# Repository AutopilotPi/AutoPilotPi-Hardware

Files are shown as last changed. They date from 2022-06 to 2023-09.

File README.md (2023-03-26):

# [ENGLISH](https://github.com/Ncerzzk/AutoPilotPi-Hardware/blob/master/README_EN.md)
# AutoPilotPi-Hardware

AutoPilotPi 是一个能够运行 PX4 等自动驾驶固件的单板计算机(SBC)。与通用的 SBC（如树莓派）不同，AutoPilotPi 集成了多种传感器（IMU、磁罗盘、气压计等），因此无需额外的接线即可使用，对于微型飞行器和电路洁癖患者来说非常友好。

AutoPilotPi 使用 V3s 处理器，虽然 V3s 不是性能强大的处理器，但如果能够证明 PX4 能在这些性能较弱的 Linux 处理器上运行，则对于性能更强的处理器来说更加不在话下了。

与传统基于 MCU 的自动驾驶固件不同，使用 Linux 系统的优势在于支持更多的开发语言和工具链，可以更方便地进行二次开发和调试。同时，开启了软实时后的内核基本可以满足 PX4 的实时性要求。

## 接口与传感器

- ICM20600：六轴惯性测量单元
- QMC5883L：三轴磁罗盘
- SPL06：气压高度传感器
- 3 个串口(U0、U1、U2，其中 U0 用于 Linux 调试)
- 1 个 I2C 接口
- 1 个 SPI 接口
- 最多 9 个 PWM 通道

## 特点

- 封装对手焊友好 (EQFP-128)
- 内置 DRAM
- 价格较为便宜

## 相关项目

- V3s 的 Linux 内核：https://github.com/Ncerzzk/linux
- 使用该项目的四旋翼飞行器 (WIP)：https://github.com/Ncerzzk/V3s_Quadrotor
- 该项目的 PX4 分支（部分提交尚未被官方 PX4 接受）：https://github.com/Ncerzzk/PX4-Autopilot
- FPGA 的 HDL 代码：https://github.com/Ncerzzk/I2C_PWM
- Wiki：https://github.com/Ncerzzk/AutoPilotPi-Hardware/wiki

## Images
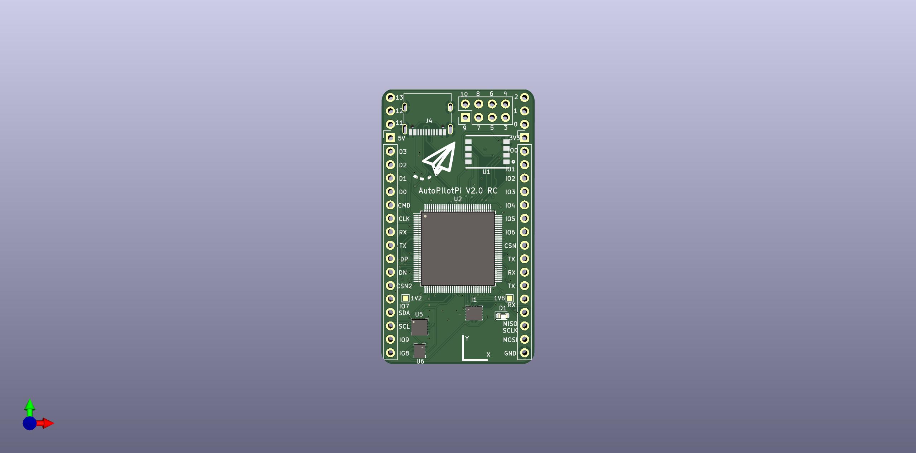
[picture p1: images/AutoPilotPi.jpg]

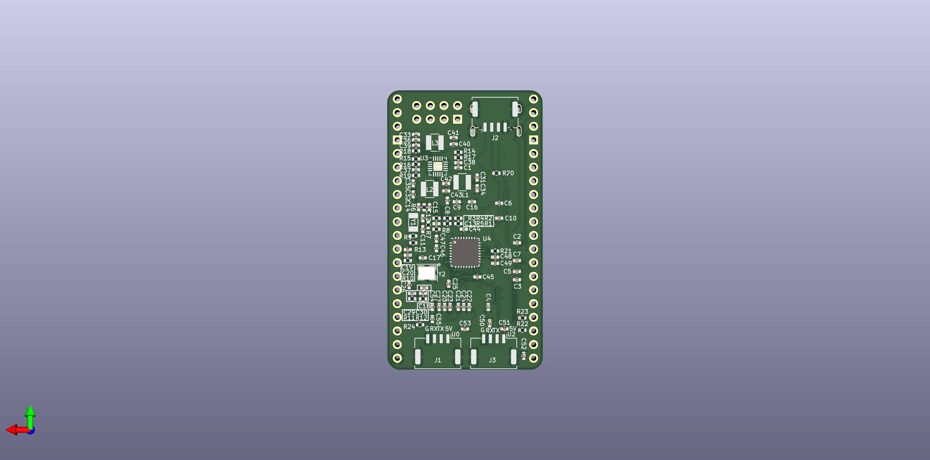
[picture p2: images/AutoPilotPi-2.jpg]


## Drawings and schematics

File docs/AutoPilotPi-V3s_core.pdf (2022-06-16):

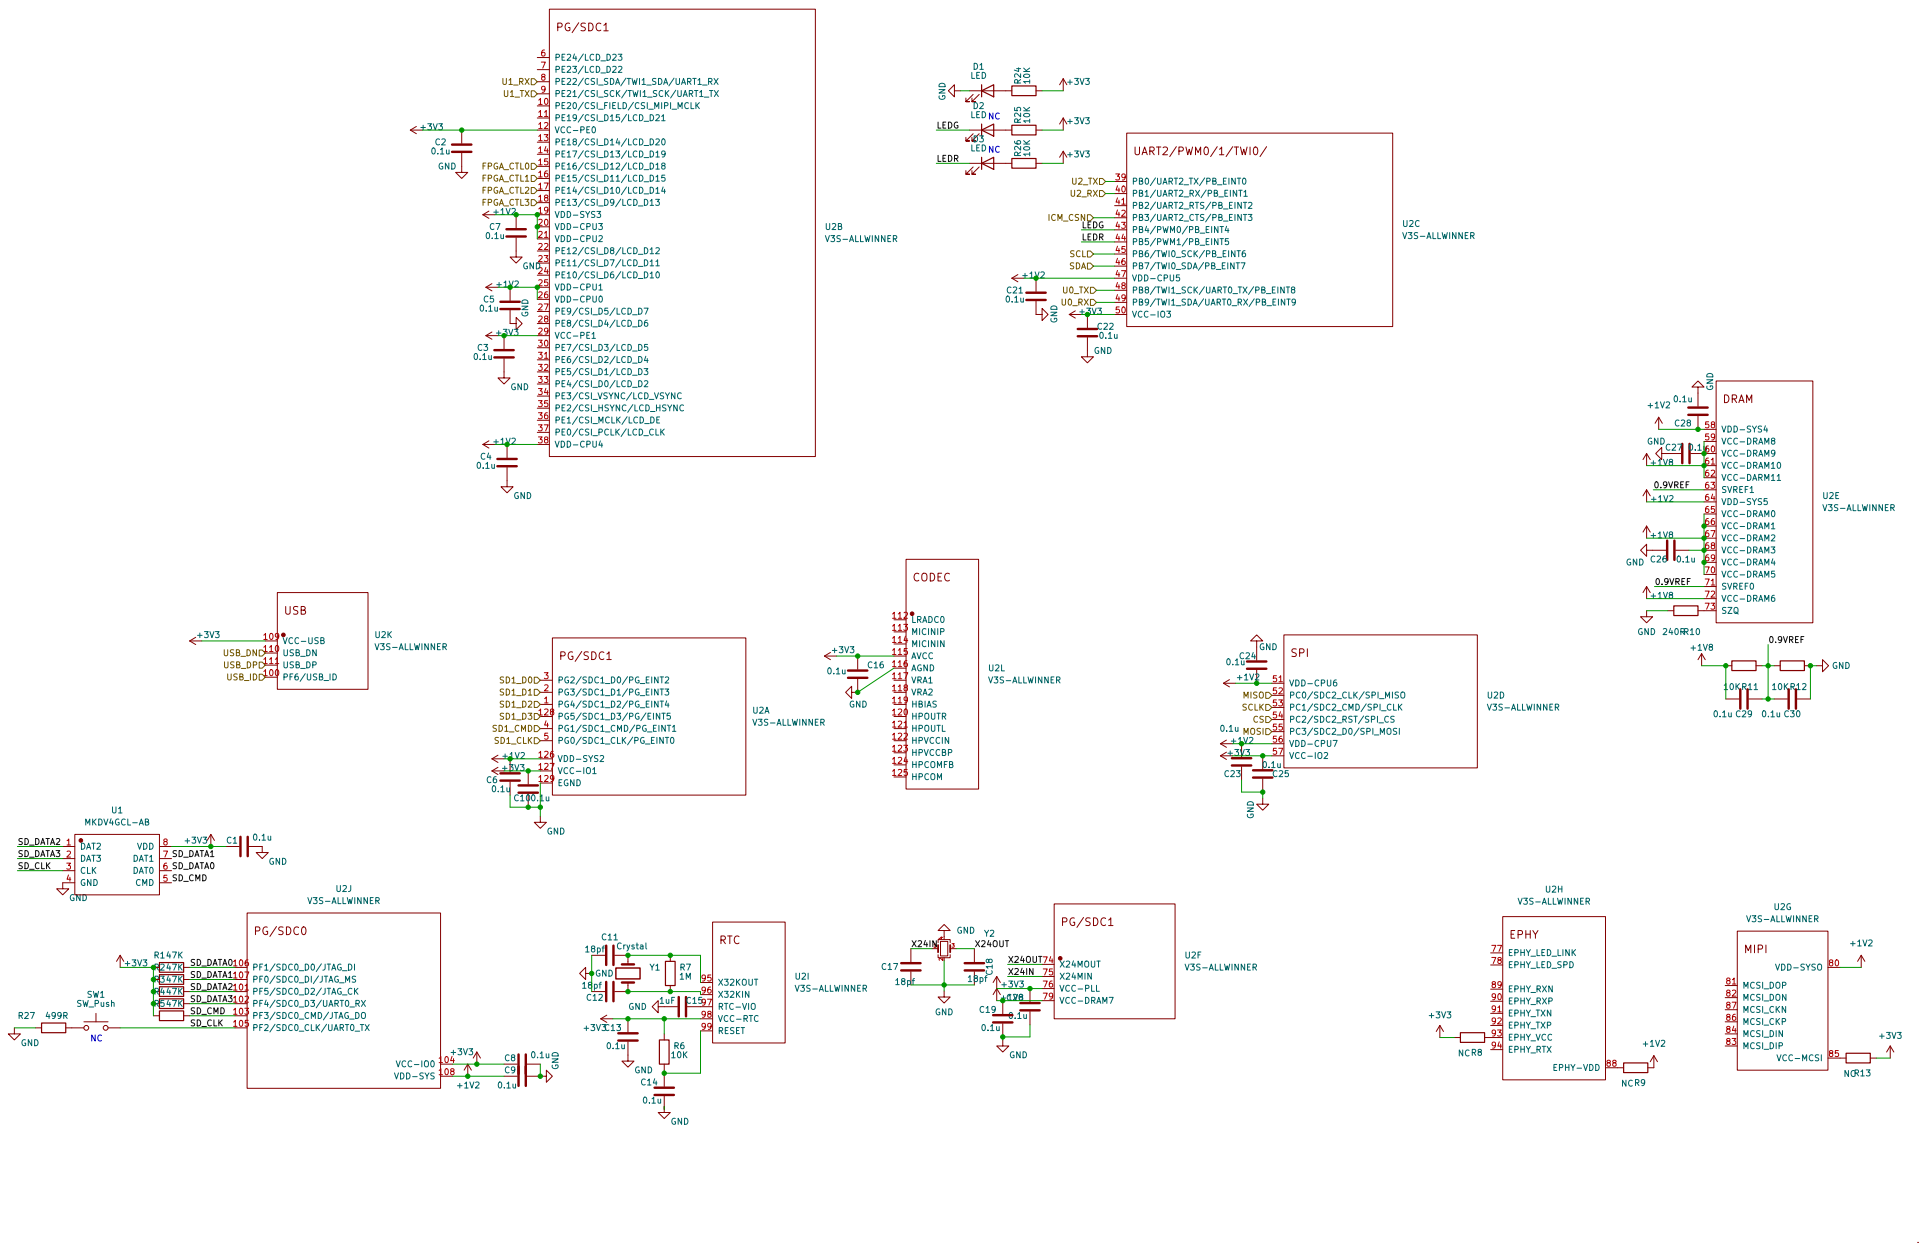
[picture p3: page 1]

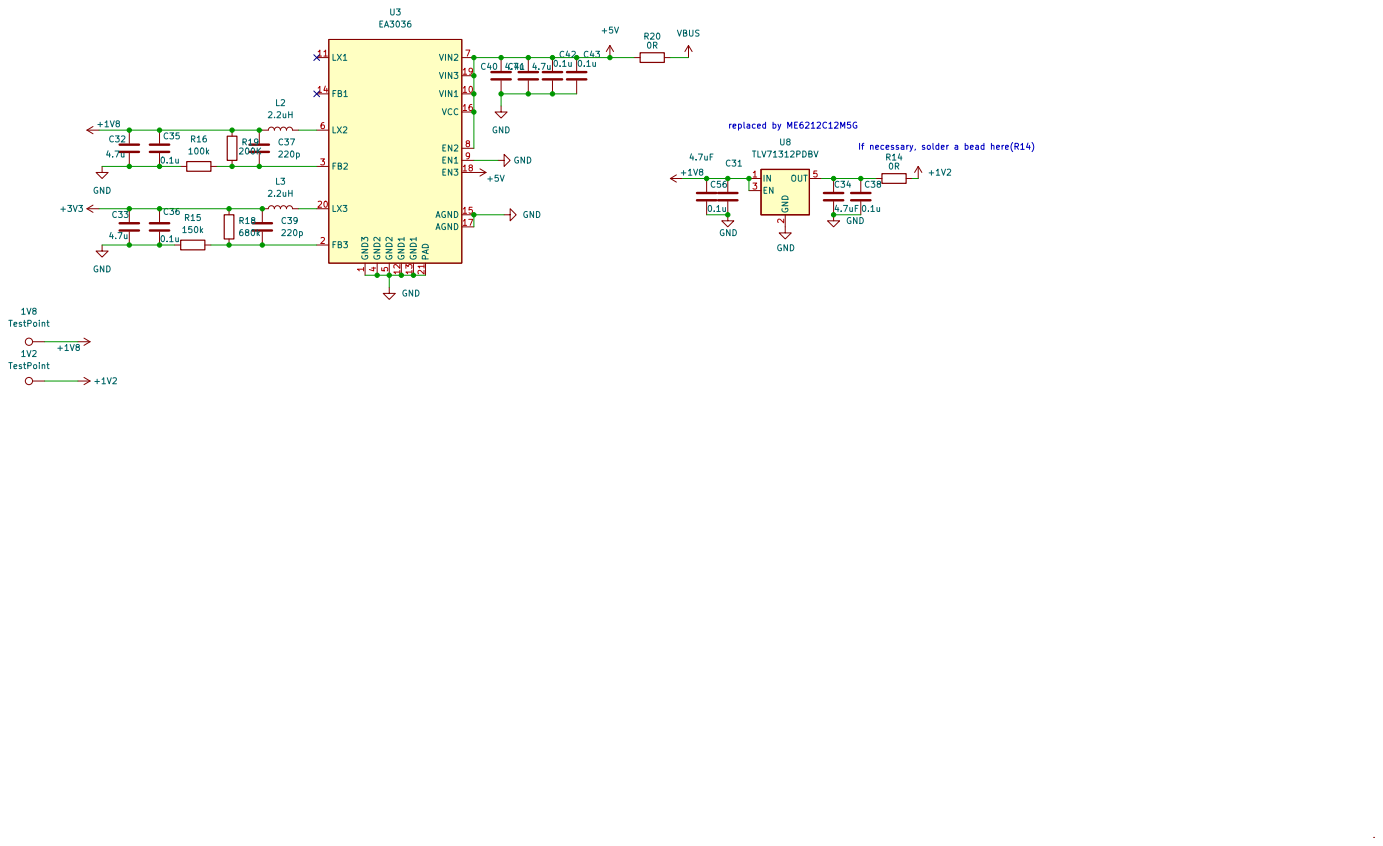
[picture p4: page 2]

2 EN 3 OUT 5 U8 TLV71312PDBV GND GND

If necessary, solder a bead here(R14)

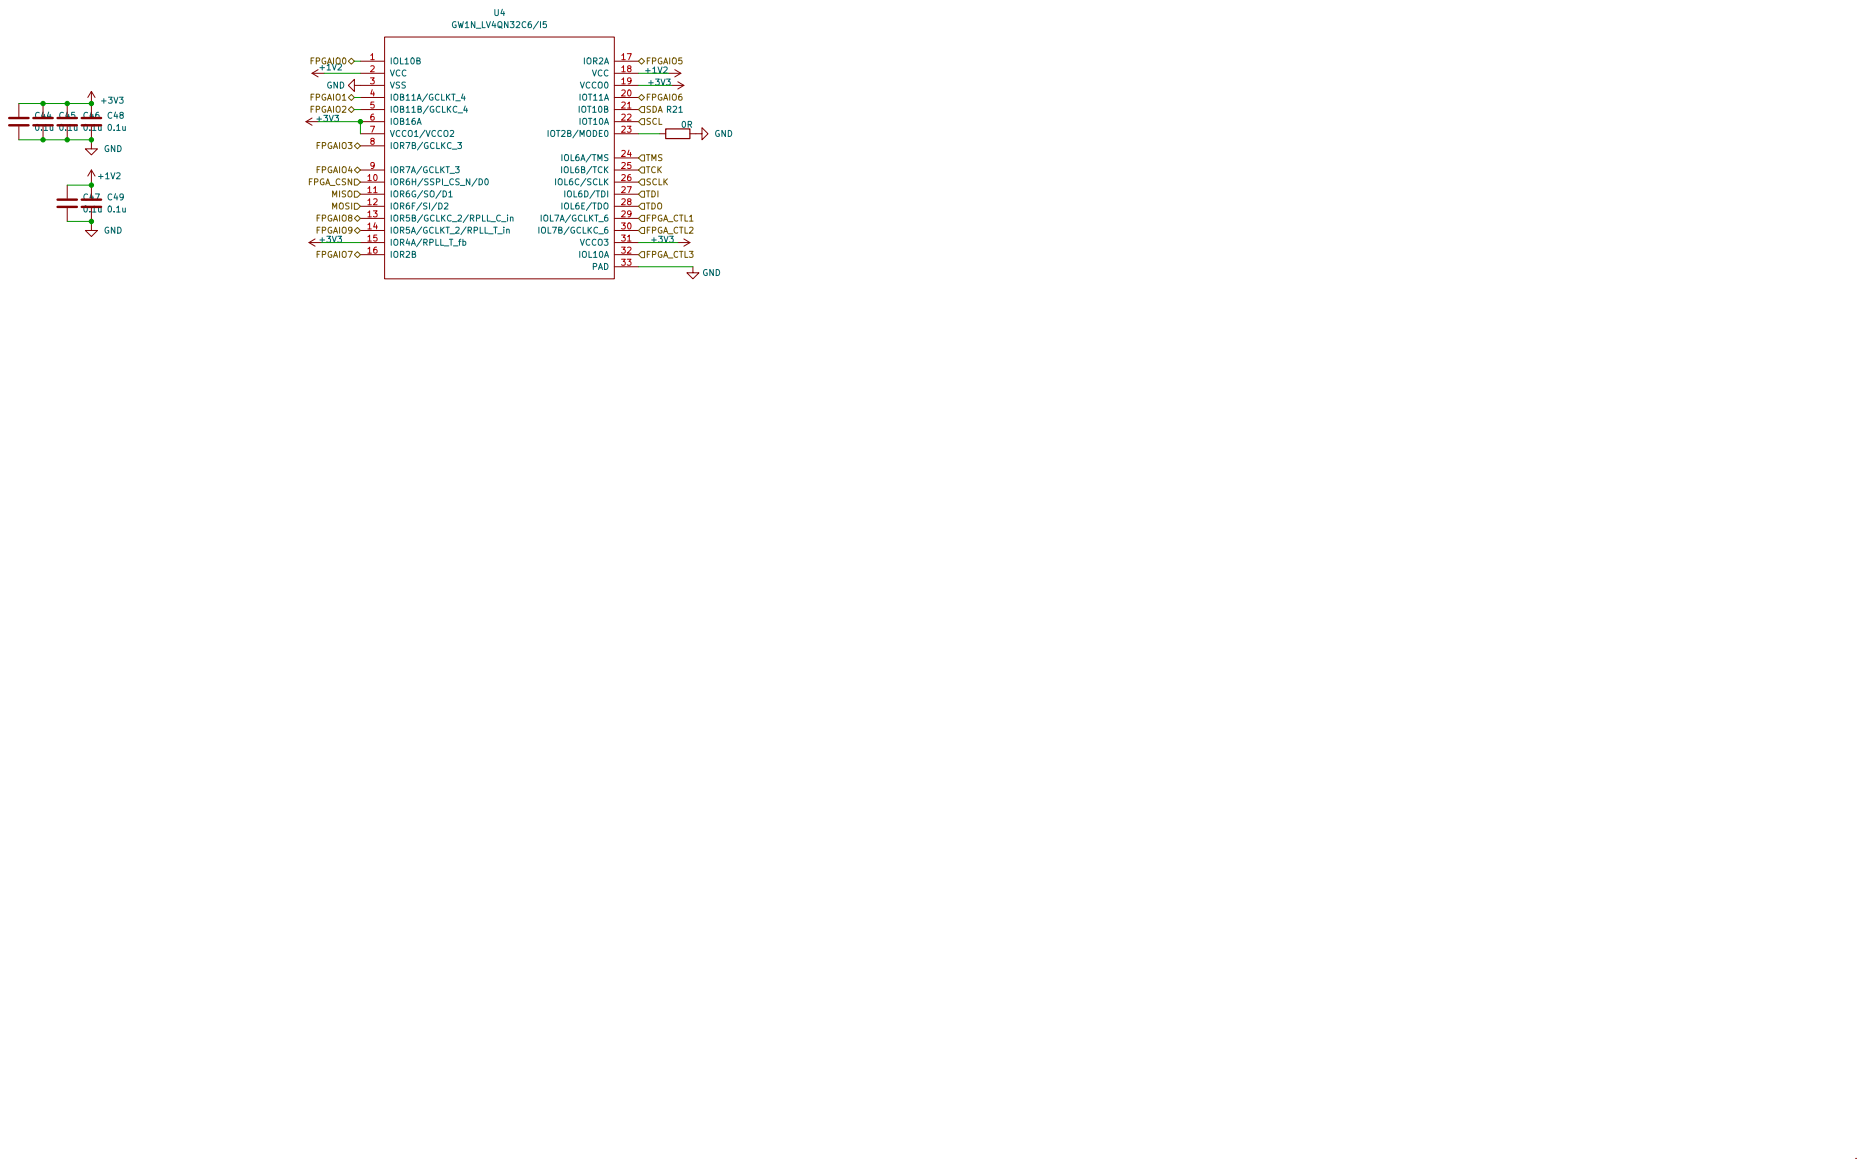
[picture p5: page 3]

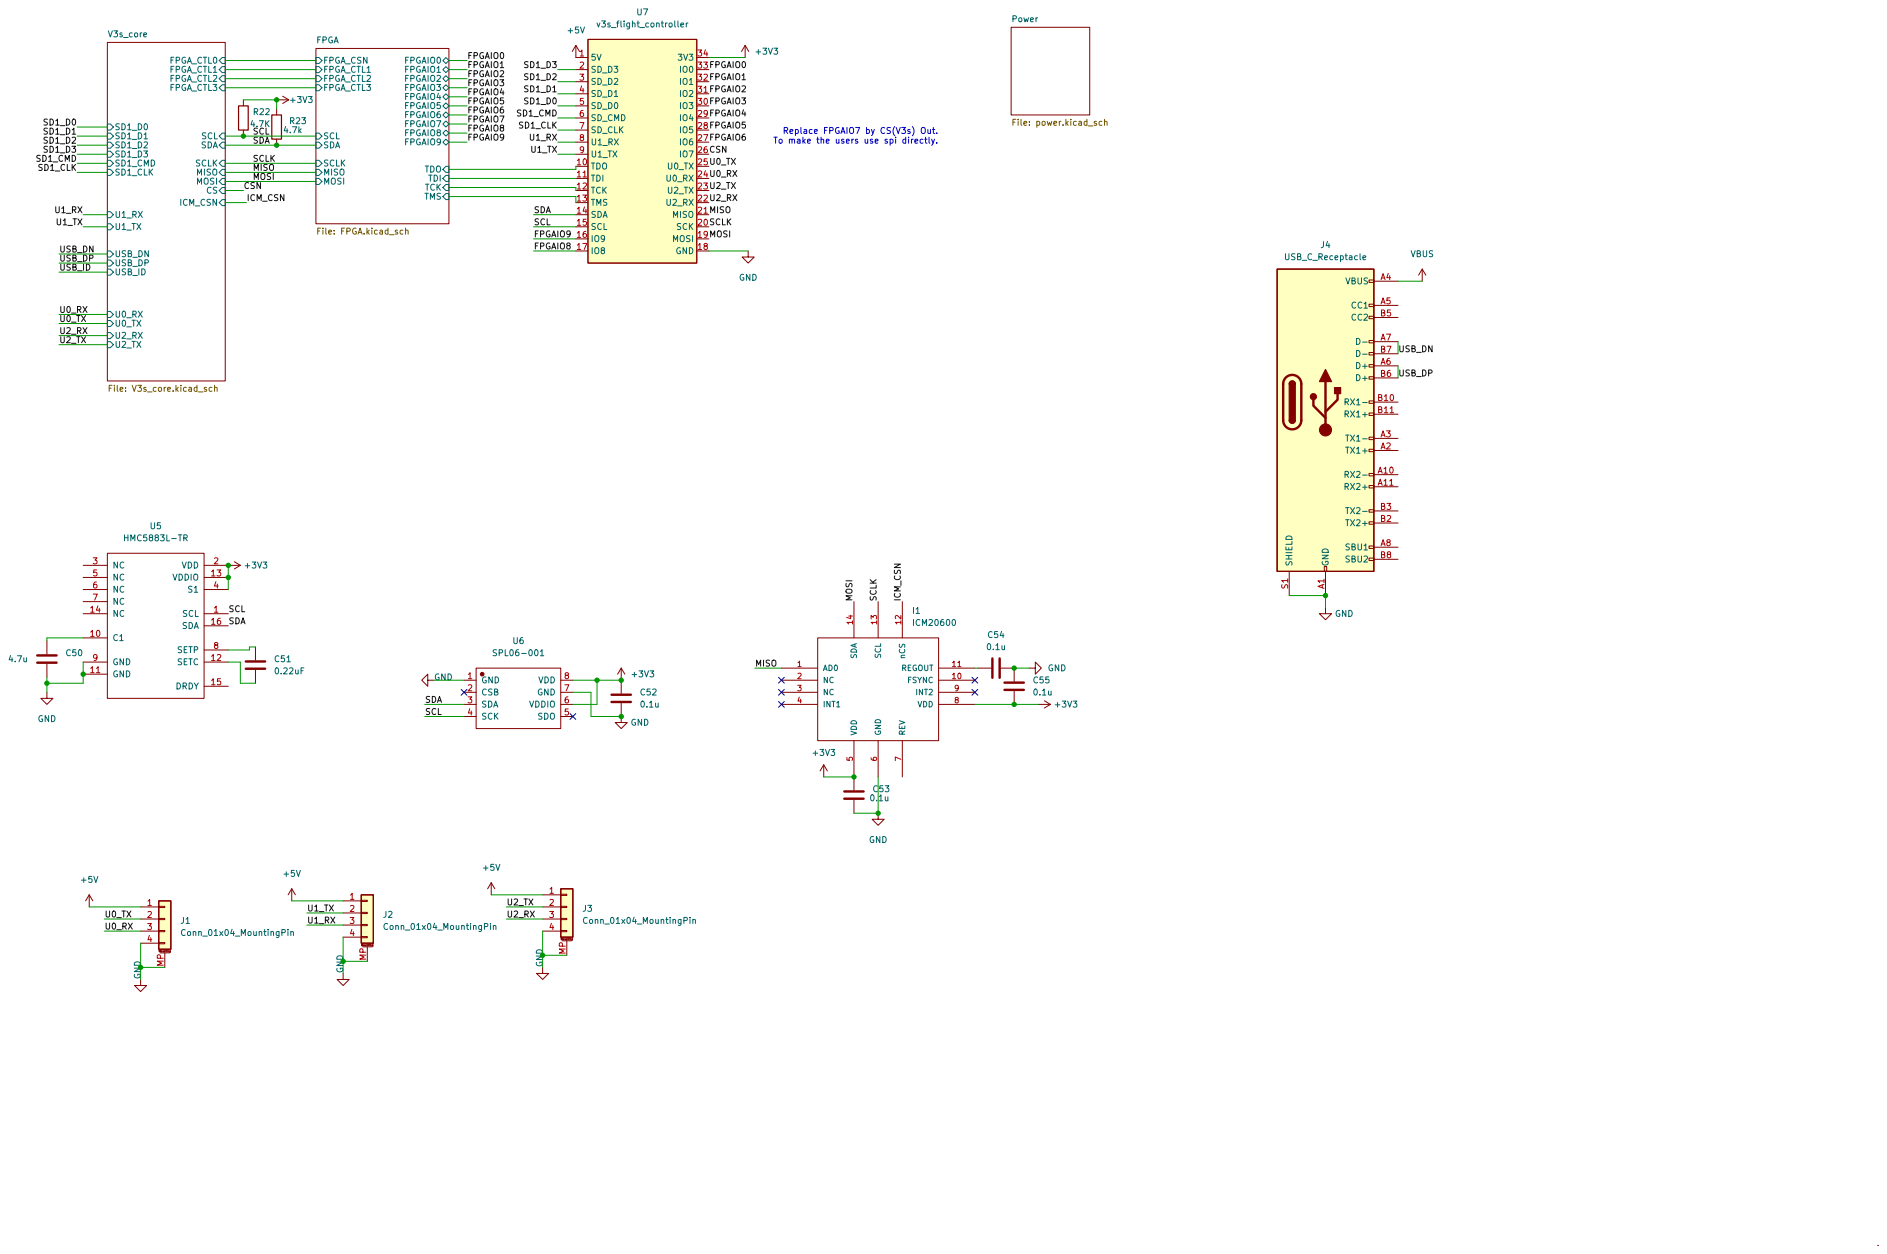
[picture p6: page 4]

To make the users use spi directly.

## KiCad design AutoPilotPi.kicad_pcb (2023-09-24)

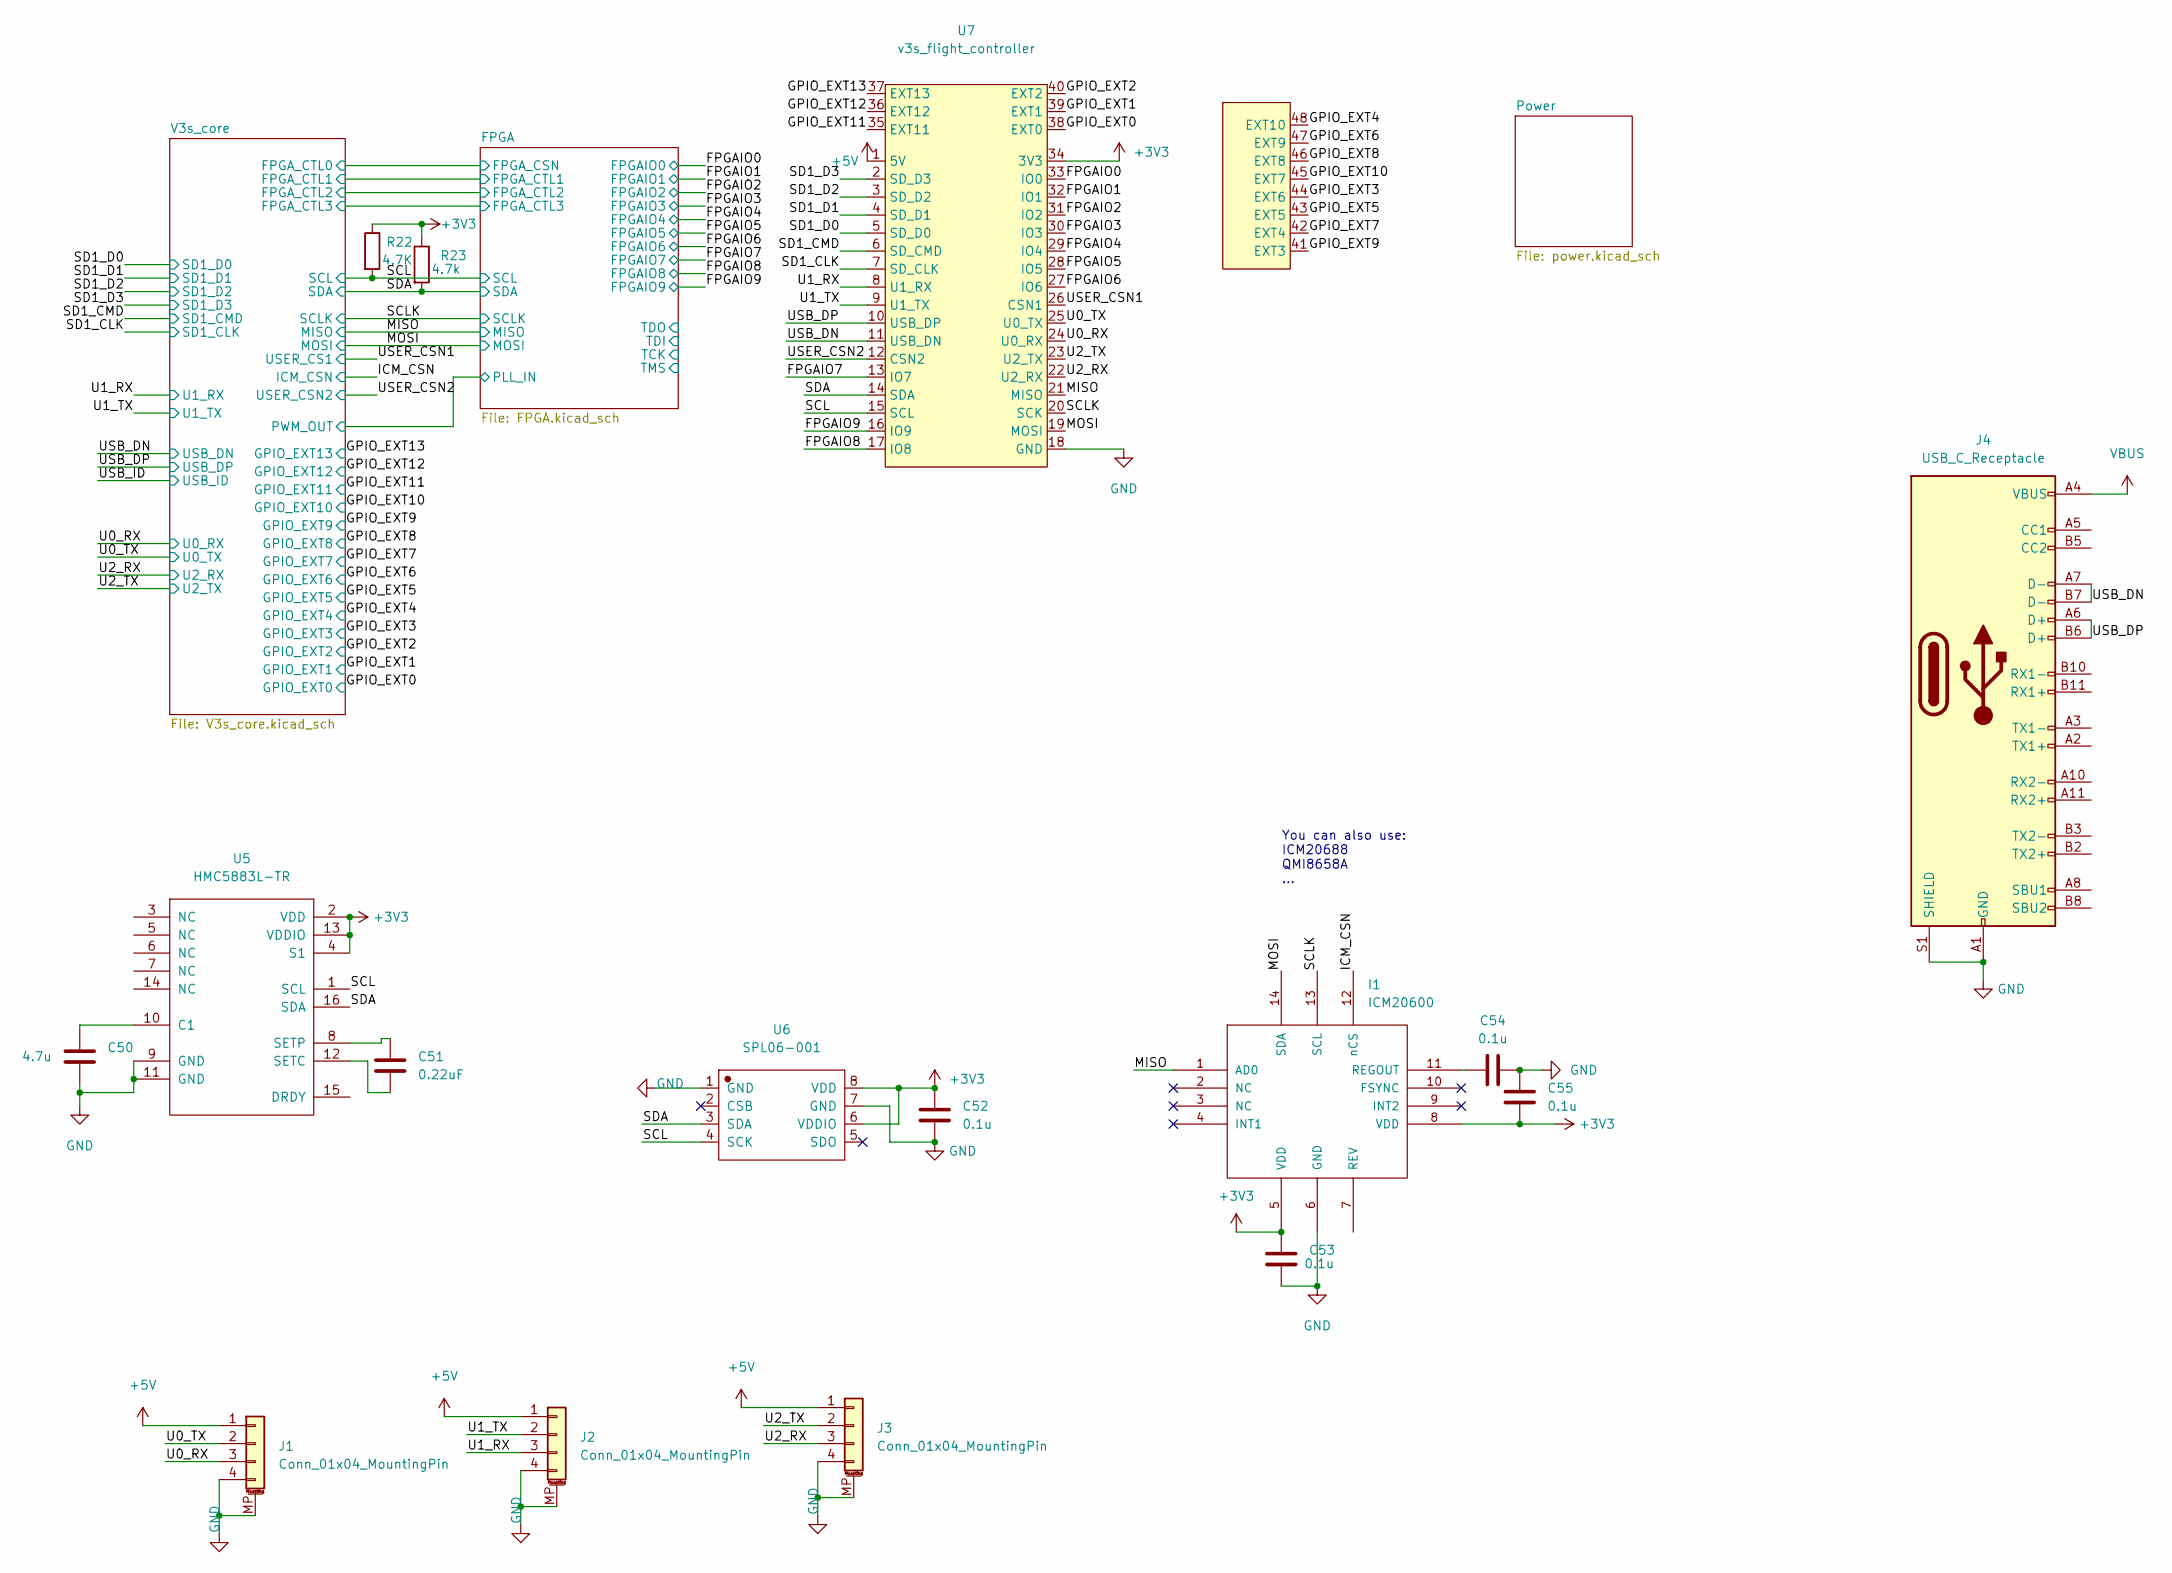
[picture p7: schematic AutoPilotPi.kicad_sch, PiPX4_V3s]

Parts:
C50: 4.7u; C_0402_1005Metric
C51: 0.22uF; C_0402_1005Metric
C52, C53, C54, C55: 0.1u; C_0402_1005Metric
I1: ICM20600; Bosch_LGA-14_3x2.5mm_P0.5mm
J1, J2, J3: Conn_01x04_MountingPin; Molex_CLIK-Mate_502382-0470_1x04-1MP_P1.25mm_Vertical
J4: USB_C_Receptacle; USB_C_Receptacle_Palconn_UTC16-G
R22: 4.7K; R_0402_1005Metric
R23: 4.7k; R_0402_1005Metric
U5: HMC5883L-TR; LGA-16_3x3mm_P0.5mm
U6: SPL06-001; Bosch_LGA-8_2x2.5mm_P0.65mm_ClockwisePinNumbering
U7: v3s_flight_controller; Flight_Core

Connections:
+3V3: C52.1, C53.2, C55.2, I1.5 (VDD), I1.8 (VDD), R22.1, R23.1, U5.2 (VDD), U5.4 (S1), U5.13 (VDDIO), U6.6 (VDDIO), U6.8 (VDD), U7.34 (3V3); also elsewhere on the board
+5V: J1.1, J2.1, J3.1, U7.1 (5V); also elsewhere on the board
/FPGAIO0: U7.33 (IO0); also elsewhere on the board
/FPGAIO1: U7.32 (IO1); also elsewhere on the board
/FPGAIO2: U7.31 (IO2); also elsewhere on the board
/FPGAIO3: U7.30 (IO3); also elsewhere on the board
/FPGAIO4: U7.29 (IO4); also elsewhere on the board
/FPGAIO5: U7.28 (IO5); also elsewhere on the board
/FPGAIO6: U7.27 (IO6); also elsewhere on the board
/FPGAIO7: U7.13 (IO7); also elsewhere on the board
/FPGAIO8: U7.17 (IO8); also elsewhere on the board
/FPGAIO9: U7.16 (IO9); also elsewhere on the board
/GPIO_EXT0: U7.38 (EXT0); also elsewhere on the board
/GPIO_EXT1: U7.39 (EXT1); also elsewhere on the board
/GPIO_EXT2: U7.40 (EXT2); also elsewhere on the board
/GPIO_EXT3: U7.44 (EXT6); also elsewhere on the board
/GPIO_EXT4: U7.48 (EXT10); also elsewhere on the board
/GPIO_EXT5: U7.43 (EXT5); also elsewhere on the board
/GPIO_EXT6: U7.47 (EXT9); also elsewhere on the board
/GPIO_EXT7: U7.42 (EXT4); also elsewhere on the board
/GPIO_EXT8: U7.46 (EXT8); also elsewhere on the board
/GPIO_EXT9: U7.41 (EXT3); also elsewhere on the board
/GPIO_EXT10: U7.45 (EXT7); also elsewhere on the board
/GPIO_EXT11: U7.35 (EXT11); also elsewhere on the board
/GPIO_EXT12: U7.36 (EXT12); also elsewhere on the board
/GPIO_EXT13: U7.37 (EXT13); also elsewhere on the board
/ICM_CSN: I1.12 (nCS); also elsewhere on the board
/MISO: I1.1 (AD0), U7.21 (MISO); also elsewhere on the board
/MOSI: I1.14 (SDA), U7.19 (MOSI); also elsewhere on the board
/SCL: R22.2, U5.1 (SCL), U6.4 (SCK), U7.15 (SCL); also elsewhere on the board
/SCLK: I1.13 (SCL), U7.20 (SCK); also elsewhere on the board
/SD1_CLK: U7.7 (SD_CLK); also elsewhere on the board
/SD1_CMD: U7.6 (SD_CMD); also elsewhere on the board
/SD1_D0: U7.5 (SD_D0); also elsewhere on the board
/SD1_D1: U7.4 (SD_D1); also elsewhere on the board
/SD1_D2: U7.3 (SD_D2); also elsewhere on the board
/SD1_D3: U7.2 (SD_D3); also elsewhere on the board
/SDA: R23.2, U5.16 (SDA), U6.3 (SDA), U7.14 (SDA); also elsewhere on the board
/U0_RX: J1.3, U7.24 (U0_RX); also elsewhere on the board
/U0_TX: J1.2, U7.25 (U0_TX); also elsewhere on the board
/U1_RX: J2.3, U7.8 (U1_RX); also elsewhere on the board
/U1_TX: J2.2, U7.9 (U1_TX); also elsewhere on the board
/U2_RX: J3.3, U7.22 (U2_RX); also elsewhere on the board
/U2_TX: J3.2, U7.23 (U2_TX); also elsewhere on the board
/USB_DN: J4.A7 (D-), J4.B7 (D-), U7.11 (USB_DN); also elsewhere on the board
/USB_DP: J4.A6 (D+), J4.B6 (D+), U7.10 (USB_DP); also elsewhere on the board
/USER_CSN1: U7.26 (CSN1); also elsewhere on the board
/USER_CSN2: U7.12 (CSN2); also elsewhere on the board
GND: C50.2, C52.2, C53.1, C54.1, C55.1, I1.6 (GND), J1.4, J1.MP (MountPin), J2.4, J2.MP (MountPin), J3.4, J3.MP (MountPin), J4.A1 (GND), J4.A12 (GND), J4.B1 (GND), J4.B12 (GND), J4.S1 (SHIELD), U5.9 (GND), U5.11 (GND), U6.1 (GND), U6.7 (GND), U7.18 (GND); also elsewhere on the board
unnamed: C50.1, U5.10 (C1)
unnamed: C51.1, U5.8 (SETP)
unnamed: C51.2, U5.12 (SETC)
unnamed: C54.2, I1.11 (REGOUT)
VBUS: J4.A4 (VBUS), J4.A9 (VBUS), J4.B4 (VBUS), J4.B9 (VBUS); also elsewhere on the board

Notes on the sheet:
You can also use: ICM20688 QMI8658A ...

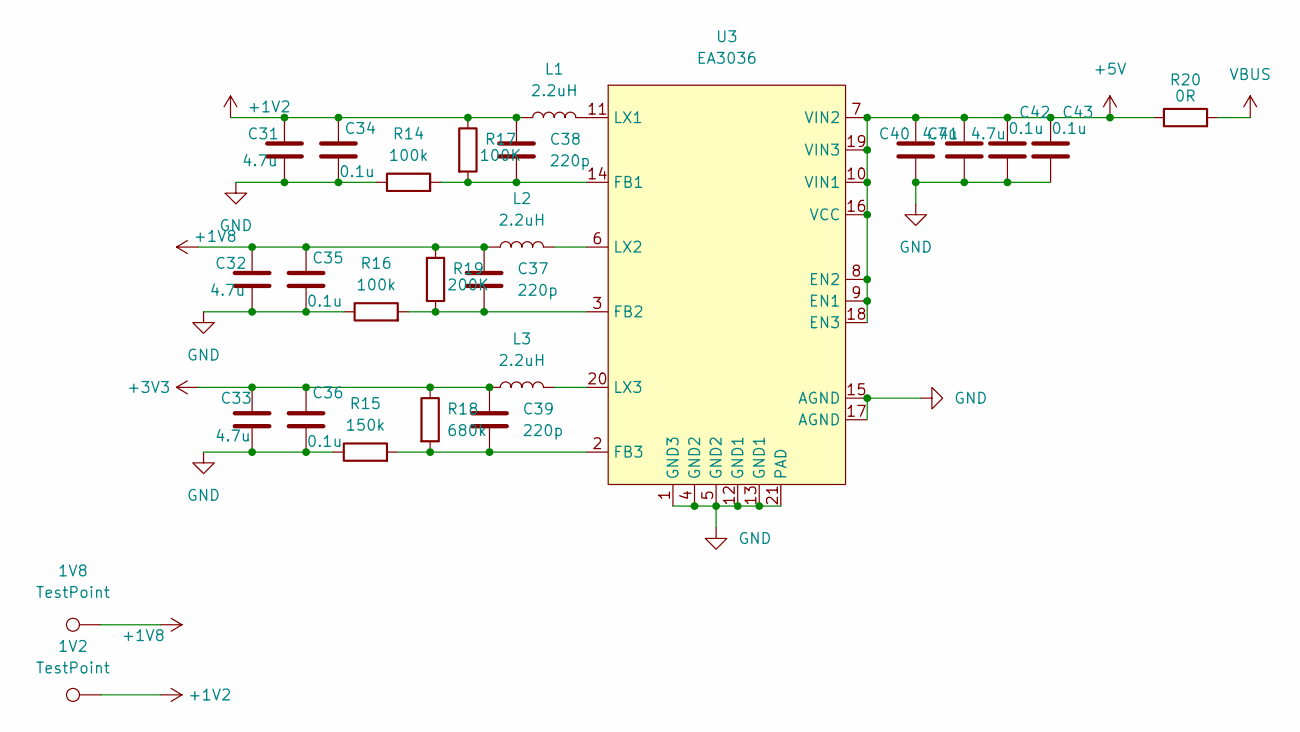
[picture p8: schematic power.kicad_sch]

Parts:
1V2, 1V8: TestPoint; TestPoint_Pad_1.0x1.0mm
C31, C32, C33, C40, C41: 4.7u; C_0402_1005Metric
C34, C35, C36, C42, C43: 0.1u; C_0402_1005Metric
C37, C38, C39: 220p; C_0402_1005Metric
L1, L2, L3: 2.2uH; L_Abracon_ASPI-3012S
R14, R16: 100k; R_0402_1005Metric
R15: 150k; R_0402_1005Metric
R17: 100K; R_0402_1005Metric
R18: 680k; R_0402_1005Metric
R19: 200K; R_0402_1005Metric
R20: 0R; R_0402_1005Metric
U3: EA3036; QFN-20-1EP_3x3mm_P0.4mm_EP1.65x1.65mm

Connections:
+1V2: 1V2.1, C31.1, C34.1, C38.1, L1.1, R17.1; also elsewhere on the board
+1V8: 1V8.1, C32.1, C35.1, C37.1, L2.1, R19.1; also elsewhere on the board
+3V3: C33.1, C36.1, C39.1, L3.1, R18.1; also elsewhere on the board
+5V: C40.1, C41.1, C42.1, C43.1, R20.1, U3.7 (VIN2), U3.8 (EN2), U3.9 (EN1), U3.10 (VIN1), U3.16 (VCC), U3.18 (EN3), U3.19 (VIN3); also elsewhere on the board
GND: C31.2, C32.2, C33.2, C34.2, C35.2, C36.2, C40.2, C41.2, C42.2, C43.2, R14.1, R15.1, R16.1, U3.1 (GND3), U3.4 (GND2), U3.5 (GND2), U3.12 (GND1), U3.13 (GND1), U3.15 (AGND), U3.17 (AGND), U3.21 (PAD); also elsewhere on the board
unnamed: C37.2, R16.2, R19.2, U3.3 (FB2)
unnamed: C38.2, R14.2, R17.2, U3.14 (FB1)
unnamed: C39.2, R15.2, R18.2, U3.2 (FB3)
unnamed: L1.2, U3.11 (LX1)
unnamed: L2.2, U3.6 (LX2)
unnamed: L3.2, U3.20 (LX3)
VBUS: R20.2; also elsewhere on the board

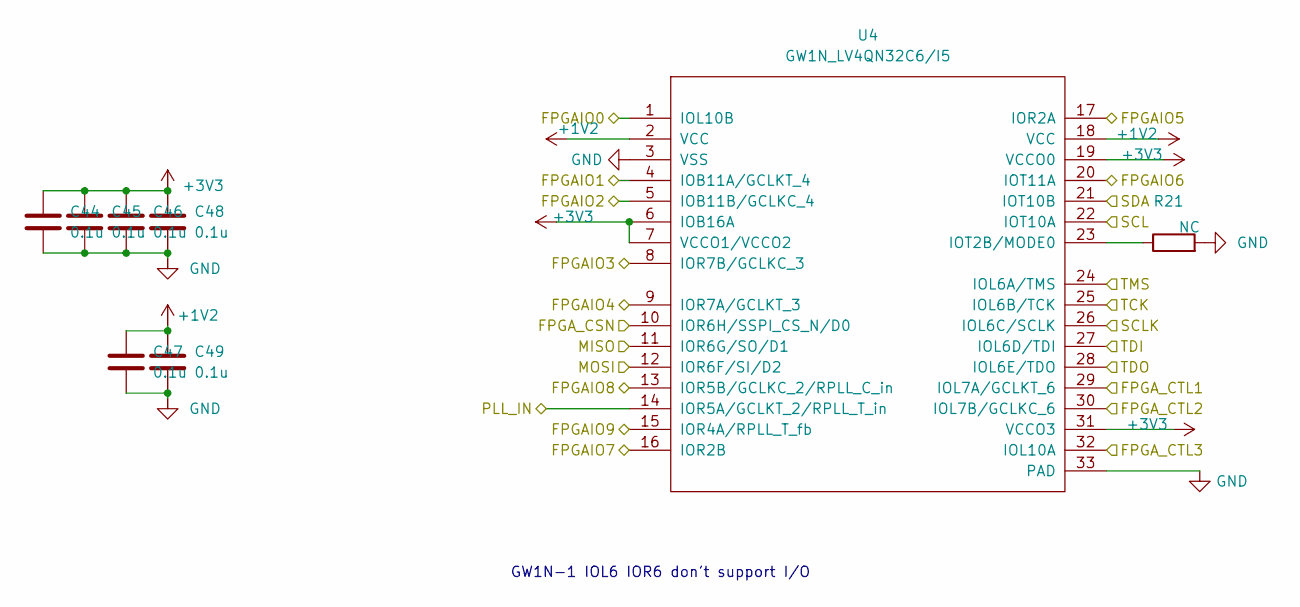
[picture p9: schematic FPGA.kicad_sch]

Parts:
C44, C45, C46, C47, C48, C49: 0.1u; C_0402_1005Metric
R21: NC; R_0402_1005Metric
U4: GW1N_LV4QN32C6/I5; QFN-32-1EP_5x5mm_P0.5mm_EP3.45x3.45mm

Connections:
+1V2: C47.1, C49.1, U4.2 (VCC), U4.18 (VCC); also elsewhere on the board
+3V3: C44.1, C45.1, C46.1, C48.1, U4.6 (IOB16A), U4.7 (VCCO1/VCCO2), U4.19 (VCCO0), U4.31 (VCCO3); also elsewhere on the board
/FPGA/FPGA_CSN: U4.10 (IOR6H/SSPI_CS_N/D0); also elsewhere on the board
/FPGA/FPGA_CTL1: U4.29 (IOL7A/GCLKT_6); also elsewhere on the board
/FPGA/FPGA_CTL2: U4.30 (IOL7B/GCLKC_6); also elsewhere on the board
/FPGA/FPGA_CTL3: U4.32 (IOL10A); also elsewhere on the board
/FPGA/PLL_IN: U4.14 (IOR5A/GCLKT_2/RPLL_T_in); also elsewhere on the board
/FPGA/TCK: U4.25 (IOL6B/TCK)
/FPGA/TDI: U4.27 (IOL6D/TDI)
/FPGA/TDO: U4.28 (IOL6E/TDO)
/FPGA/TMS: U4.24 (IOL6A/TMS)
/FPGAIO0: U4.1 (IOL10B); also elsewhere on the board
/FPGAIO1: U4.4 (IOB11A/GCLKT_4); also elsewhere on the board
/FPGAIO2: U4.5 (IOB11B/GCLKC_4); also elsewhere on the board
/FPGAIO3: U4.8 (IOR7B/GCLKC_3); also elsewhere on the board
/FPGAIO4: U4.9 (IOR7A/GCLKT_3); also elsewhere on the board
/FPGAIO5: U4.17 (IOR2A); also elsewhere on the board
/FPGAIO6: U4.20 (IOT11A); also elsewhere on the board
/FPGAIO7: U4.16 (IOR2B); also elsewhere on the board
/FPGAIO8: U4.13 (IOR5B/GCLKC_2/RPLL_C_in); also elsewhere on the board
/FPGAIO9: U4.15 (IOR4A/RPLL_T_fb); also elsewhere on the board
/MISO: U4.11 (IOR6G/SO/D1); also elsewhere on the board
/MOSI: U4.12 (IOR6F/SI/D2); also elsewhere on the board
/SCL: U4.22 (IOT10A); also elsewhere on the board
/SCLK: U4.26 (IOL6C/SCLK); also elsewhere on the board
/SDA: U4.21 (IOT10B); also elsewhere on the board
GND: C44.2, C45.2, C46.2, C47.2, C48.2, C49.2, R21.2, U4.3 (VSS), U4.33 (PAD); also elsewhere on the board
unnamed: R21.1, U4.23 (IOT2B/MODE0)

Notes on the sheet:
GW1N-1 IOL6 IOR6 don't support I/O

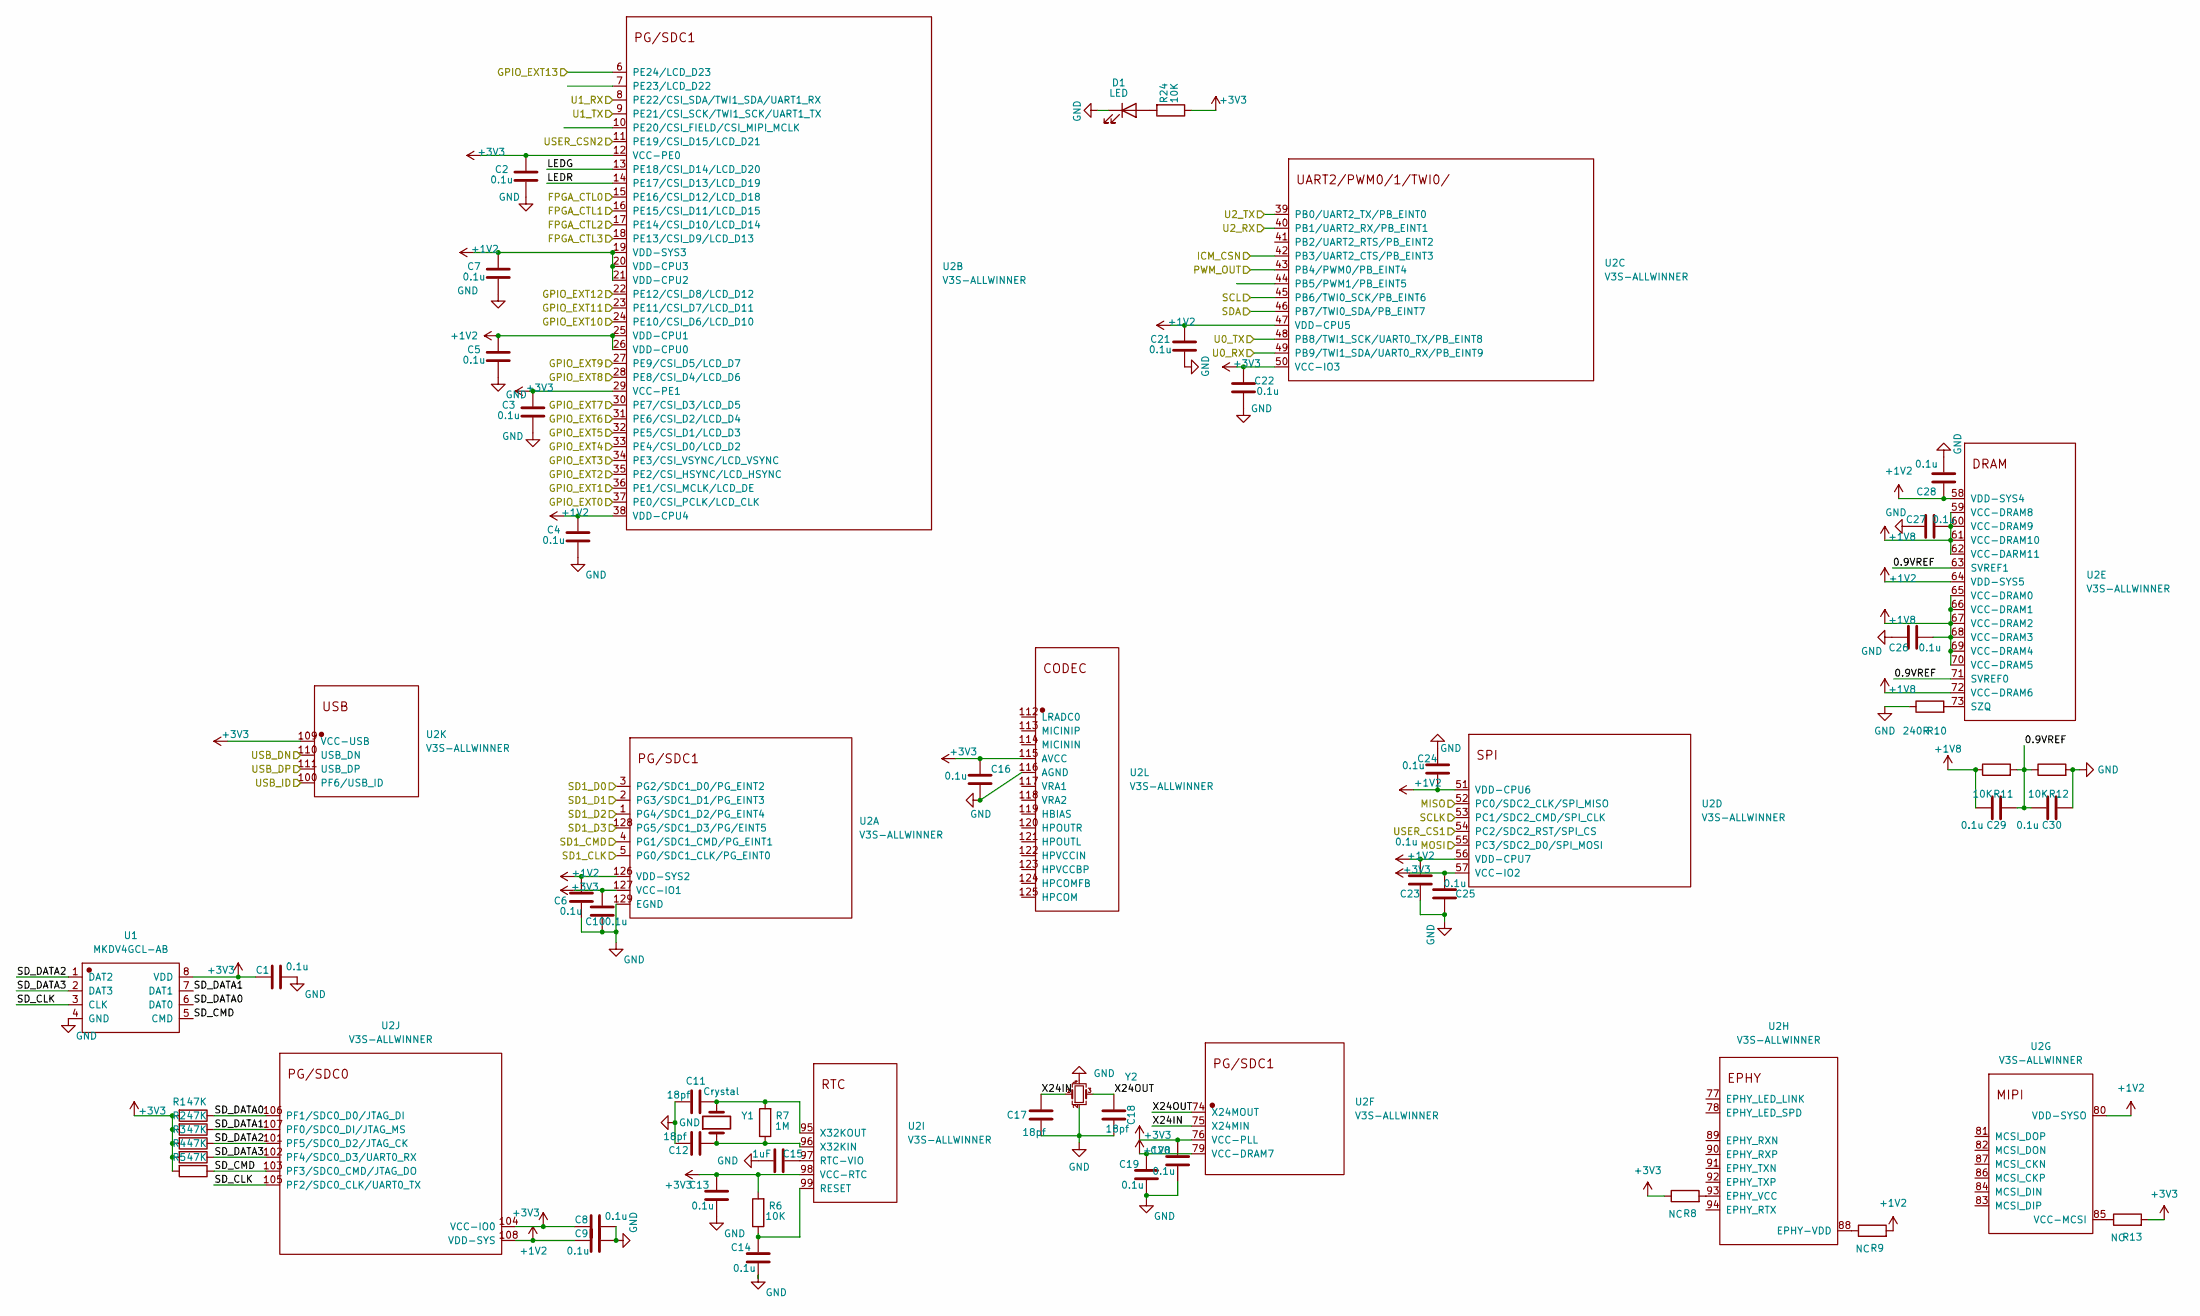
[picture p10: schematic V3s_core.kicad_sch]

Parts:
C1, C2, C3, C4, C5, C6, C7, C8, C9, C10, C13, C14, C16, C19, C20, C21, C22, C23, C24, C25, C26, C27, C28, C29, C30: 0.1u; C_0402_1005Metric
C11, C12, C17, C18: 18pf; C_0402_1005Metric
C15: 1uF; C_0402_1005Metric
D1: LED; LED_0603_1608Metric
R1, R2, R3, R4, R5: 47K; R_0402_1005Metric
R6, R11, R12, R24: 10K; R_0402_1005Metric
R7: 1M; R_0402_1005Metric
R8, R9, R13: NC; R_0402_1005Metric
R10: 240R; R_0402_1005Metric
U1: MKDV4GCL-AB; LGA-8_L8.0-W6.0-BL_MKDV4GIL-AS
U2: V3S-ALLWINNER; EQFP-128_14x14mm_P0.4mm
Y1: Crystal; Crystal_SMD_3215-2Pin_3.2x1.5mm
Y2: Crystal_GND24_Small; Crystal_SMD_EuroQuartz_MT-4Pin_3.2x2.5mm

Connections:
+1V2: C4.1, C5.1, C6.1, C7.1, C9.2, C21.1, C23.1, C24.2, C28.2, R9.2, U2.19 (VDD-SYS3), U2.20 (VDD-CPU3), U2.21 (VDD-CPU2), U2.25 (VDD-CPU1), U2.26 (VDD-CPU0), U2.38 (VDD-CPU4), U2.47 (VDD-CPU5), U2.51 (VDD-CPU6), U2.56 (VDD-CPU7), U2.58 (VDD-SYS4), U2.64 (VDD-SYS5), U2.80 (VDD-SYSO), U2.108 (VDD-SYS), U2.126 (VDD-SYS2); also elsewhere on the board
+1V8: C19.2, C26.1, C27.1, C29.1, R11.1, U2.59 (VCC-DRAM8), U2.60 (VCC-DRAM9), U2.61 (VCC-DRAM10), U2.62 (VCC-DARM11), U2.65 (VCC-DRAM0), U2.66 (VCC-DRAM1), U2.67 (VCC-DRAM2), U2.68 (VCC-DRAM3), U2.69 (VCC-DRAM4), U2.70 (VCC-DRAM5), U2.72 (VCC-DRAM6), U2.79 (VCC-DRAM7); also elsewhere on the board
+3V3: C1.2, C2.1, C3.1, C8.2, C10.1, C13.2, C16.1, C20.2, C22.1, C25.1, R1.2, R2.2, R3.2, R4.2, R5.2, R6.2, R8.1, R13.2, R24.1, U1.8 (VDD), U2.12 (VCC-PE0), U2.29 (VCC-PE1), U2.50 (VCC-IO3), U2.57 (VCC-IO2), U2.76 (VCC-PLL), U2.98 (VCC-RTC), U2.104 (VCC-IO0), U2.109 (VCC-USB), U2.115 (AVCC), U2.127 (VCC-IO1); also elsewhere on the board
/FPGA/FPGA_CSN: U2.15 (PE16/CSI_D12/LCD_D18); also elsewhere on the board
/FPGA/FPGA_CTL1: U2.16 (PE15/CSI_D11/LCD_D15); also elsewhere on the board
/FPGA/FPGA_CTL2: U2.17 (PE14/CSI_D10/LCD_D14); also elsewhere on the board
/FPGA/FPGA_CTL3: U2.18 (PE13/CSI_D9/LCD_D13); also elsewhere on the board
/FPGA/PLL_IN: U2.43 (PB4/PWM0/PB_EINT4); also elsewhere on the board
/GPIO_EXT0: U2.37 (PE0/CSI_PCLK/LCD_CLK); also elsewhere on the board
/GPIO_EXT1: U2.36 (PE1/CSI_MCLK/LCD_DE); also elsewhere on the board
/GPIO_EXT2: U2.35 (PE2/CSI_HSYNC/LCD_HSYNC); also elsewhere on the board
/GPIO_EXT3: U2.34 (PE3/CSI_VSYNC/LCD_VSYNC); also elsewhere on the board
/GPIO_EXT4: U2.33 (PE4/CSI_D0/LCD_D2); also elsewhere on the board
/GPIO_EXT5: U2.32 (PE5/CSI_D1/LCD_D3); also elsewhere on the board
/GPIO_EXT6: U2.31 (PE6/CSI_D2/LCD_D4); also elsewhere on the board
/GPIO_EXT7: U2.30 (PE7/CSI_D3/LCD_D5); also elsewhere on the board
/GPIO_EXT8: U2.28 (PE8/CSI_D4/LCD_D6); also elsewhere on the board
/GPIO_EXT9: U2.27 (PE9/CSI_D5/LCD_D7); also elsewhere on the board
/GPIO_EXT10: U2.24 (PE10/CSI_D6/LCD_D10); also elsewhere on the board
/GPIO_EXT11: U2.23 (PE11/CSI_D7/LCD_D11); also elsewhere on the board
/GPIO_EXT12: U2.22 (PE12/CSI_D8/LCD_D12); also elsewhere on the board
/GPIO_EXT13: U2.6 (PE24/LCD_D23); also elsewhere on the board
/ICM_CSN: U2.42 (PB3/UART2_CTS/PB_EINT3); also elsewhere on the board
/MISO: U2.52 (PC0/SDC2_CLK/SPI_MISO); also elsewhere on the board
/MOSI: U2.55 (PC3/SDC2_D0/SPI_MOSI); also elsewhere on the board
/SCL: U2.45 (PB6/TWI0_SCK/PB_EINT6); also elsewhere on the board
/SCLK: U2.53 (PC1/SDC2_CMD/SPI_CLK); also elsewhere on the board
/SD1_CLK: U2.5 (PG0/SDC1_CLK/PG_EINT0); also elsewhere on the board
/SD1_CMD: U2.4 (PG1/SDC1_CMD/PG_EINT1); also elsewhere on the board
/SD1_D0: U2.3 (PG2/SDC1_D0/PG_EINT2); also elsewhere on the board
/SD1_D1: U2.2 (PG3/SDC1_D1/PG_EINT3); also elsewhere on the board
/SD1_D2: U2.1 (PG4/SDC1_D2/PG_EINT4); also elsewhere on the board
/SD1_D3: U2.128 (PG5/SDC1_D3/PG/EINT5); also elsewhere on the board
/SDA: U2.46 (PB7/TWI0_SDA/PB_EINT7); also elsewhere on the board
/U0_RX: U2.49 (PB9/TWI1_SDA/UART0_RX/PB_EINT9); also elsewhere on the board
/U0_TX: U2.48 (PB8/TWI1_SCK/UART0_TX/PB_EINT8); also elsewhere on the board
/U1_RX: U2.8 (PE22/CSI_SDA/TWI1_SDA/UART1_RX); also elsewhere on the board
/U1_TX: U2.9 (PE21/CSI_SCK/TWI1_SCK/UART1_TX); also elsewhere on the board
/U2_RX: U2.40 (PB1/UART2_RX/PB_EINT1); also elsewhere on the board
/U2_TX: U2.39 (PB0/UART2_TX/PB_EINT0); also elsewhere on the board
/USB_DN: U2.110 (USB_DN); also elsewhere on the board
/USB_DP: U2.111 (USB_DP); also elsewhere on the board
/USB_ID: U2.100 (PF6/USB_ID)
/USER_CSN1: U2.54 (PC2/SDC2_RST/SPI_CS); also elsewhere on the board
/USER_CSN2: U2.11 (PE19/CSI_D15/LCD_D21); also elsewhere on the board
/V3s_core/0.9VREF: C29.2, C30.1, R11.2, R12.1, U2.63 (SVREF1), U2.71 (SVREF0)
/V3s_core/LEDG: U2.13 (PE18/CSI_D14/LCD_D20)
/V3s_core/LEDR: U2.14 (PE17/CSI_D13/LCD_D19)
/V3s_core/SD_CLK: U1.3 (CLK), U2.105 (PF2/SDC0_CLK/UART0_TX)
/V3s_core/SD_CMD: R5.1, U1.5 (CMD), U2.103 (PF3/SDC0_CMD/JTAG_DO)
/V3s_core/SD_DATA0: R1.1, U1.6 (DAT0), U2.106 (PF1/SDC0_D0/JTAG_DI)
/V3s_core/SD_DATA1: R2.1, U1.7 (DAT1), U2.107 (PF0/SDC0_DI/JTAG_MS)
/V3s_core/SD_DATA2: R3.1, U1.1 (DAT2), U2.101 (PF5/SDC0_D2/JTAG_CK)
/V3s_core/SD_DATA3: R4.1, U1.2 (DAT3), U2.102 (PF4/SDC0_D3/UART0_RX)
/V3s_core/X24IN: C17.2, U2.75 (X24MIN), Y2.1
/V3s_core/X24OUT: C18.2, U2.74 (X24MOUT), Y2.3
GND: C1.1, C2.2, C3.2, C4.2, C5.2, C6.2, C7.2, C8.1, C9.1, C10.2, C11.1, C12.1, C13.1, C14.1, C15.1, C16.2, C17.1, C18.1, C19.1, C20.1, C21.2, C22.2, C23.2, C24.1, C25.2, C26.2, C27.2, C28.1, C30.2, D1.1 (K), R10.1, R12.2, U1.4 (GND), U2.116 (AGND), U2.129 (EGND), Y2.2, Y2.4; also elsewhere on the board
unnamed: C11.2, R7.2, U2.95 (X32KOUT), Y1.2
unnamed: C12.2, R7.1, U2.96 (X32KIN), Y1.1
unnamed: C14.2, R6.1, U2.99 (RESET)
unnamed: C15.2, U2.97 (RTC-VIO)
unnamed: D1.2 (A), R24.2
unnamed: R8.2, U2.93 (EPHY_VCC)
unnamed: R9.1, U2.88 (EPHY-VDD)
unnamed: R10.2, U2.73 (SZQ)
unnamed: R13.1, U2.85 (VCC-MCSI)

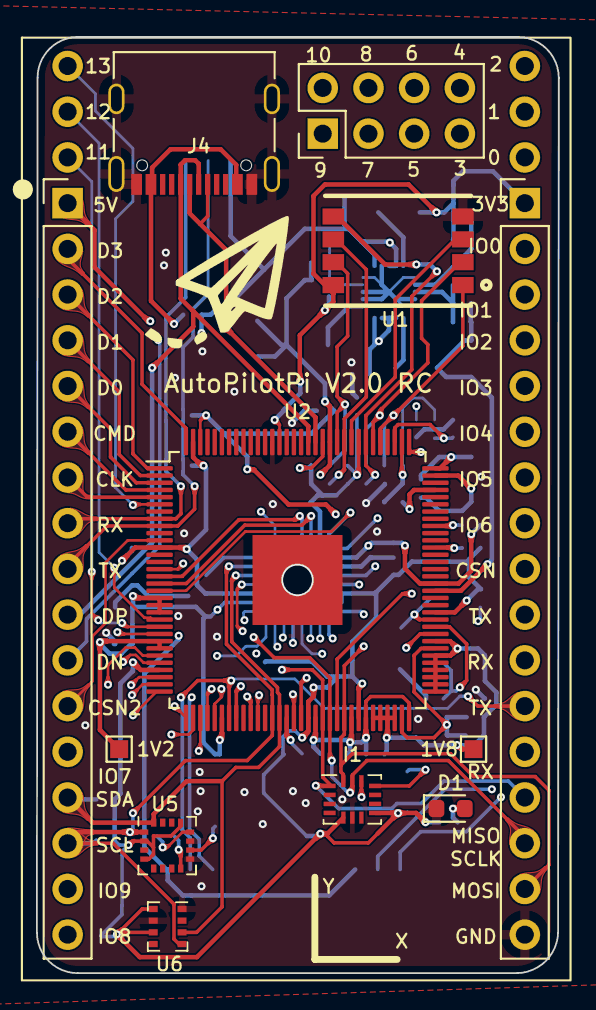
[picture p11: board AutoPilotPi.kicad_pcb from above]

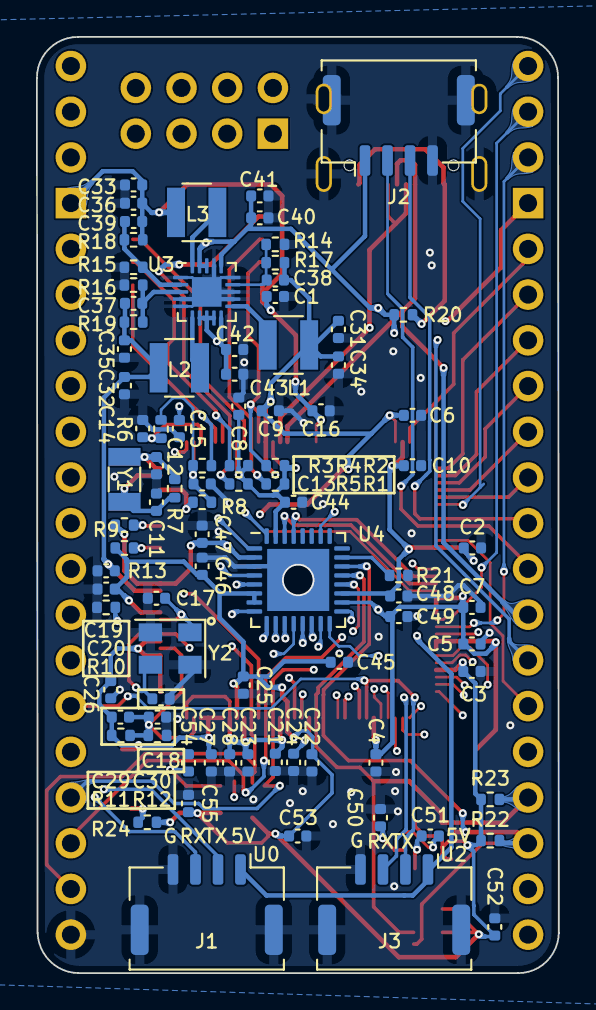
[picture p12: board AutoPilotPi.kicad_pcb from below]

Board: 4 copper layers, 29.0 x 52.0 mm, 99 parts (89 on the bottom side), 86 nets.

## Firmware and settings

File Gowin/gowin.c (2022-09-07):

#include <stdlib.h>
#include <stdio.h>
#include <stdint.h>
#include <unistd.h>

#include <fcntl.h>
#include <sys/ioctl.h>
#include <linux/types.h>
#include <linux/spi/spidev.h>

/* 
Info:	"Read Device Codes" starting on device-1...
Info:	ID code is: 0x0900281B
Info:	User code is: 0x000044CE
Info:	Status code is: 0x0001F020
Info:	Cost 0.6 second(s)
*/


typedef struct{
    uint8_t command[4];
    uint8_t len;
}gowin_command;

#define READ_ID_CODE 0x11
#define USER_CODE 0x13
#define STATUS_CODE 0x41
gowin_command COMMAND_READ_ID_CODE={{0x11,0x00,0x00,0x00},4};
gowin_command COMMAND_USER_CODE={{0x13,0x00,0x00,0x00},4};
gowin_command COMMAND_STATUS_CODE={{0x41,0x00,0x00,0x00},4};

int transfer(int _fd,uint8_t *send, uint8_t *recv, unsigned len);
uint32_t get_codes(int fd,uint8_t code);
uint32_t get_all_codes(int fd);

#define GPIO_VAL(gpio_num)      "/sys/class/gpio/gpio" gpio_num "/value"
#define CS_VAL_DEVICE                  GPIO_VAL("144")

void set_gpio(char * device,char * level){
    int fd = open(device, O_WRONLY);
    if (fd == -1) {
        printf("Unable to open %s\n", device);
    }

    if (write(fd, level, 1) != 1) {
        printf("Error writing to /sys/class/gpio/gpio144/value\n");
    }
    close(fd);
}
void set_cs(char * target){
    set_gpio(CS_VAL_DEVICE,target);
}

void give_some_fucking_sclk_cycles(){
    uint8_t buf=0xff;
    // just for making gowin fpga happy
    //int fd = open("/dev/spidev0.3", O_RDWR);
    //transfer(fd,&buf,&buf,1);
    //close(fd);
    
}

int transfer(int _fd,uint8_t *send, uint8_t *recv, unsigned len)
{
    int result=0;
	if ((send == 0) && (recv == 0)) {
		return -1;
	}

	struct spi_ioc_transfer spi_transfer={
        .tx_buf = (uint64_t)send,
        .rx_buf = (uint64_t)recv,
        .len = len,
        .speed_hz = 50000,
        .bits_per_word = 8,
    };
    
	result = ioctl(_fd, SPI_IOC_MESSAGE(1), &spi_transfer);
	if (result != (int)len) {
        printf("spi transfer error\n");
        printf("send len:%d result:%d\n", len,result);
	}

    return 0;
}


uint32_t get_codes(int fd,uint8_t code){
    uint8_t buf[8]={code};
    uint32_t result=0;
    give_some_fucking_sclk_cycles();
    transfer(fd,buf,buf,8);
    printf("get code:0x%x  :",code);
    result=(uint32_t) buf[4]<<24 |(uint32_t) buf[5] <<16 |(uint32_t) buf[6] <<8 | buf[7];
    printf("0x%x \n",result);
    return result;
}

int write_enable(int fd){
    uint8_t buf[2]={0x15};
    give_some_fucking_sclk_cycles();
    int result= transfer(fd,buf,buf,2); 
    return result;

}



int gpio_export(){
    int fd = open("/sys/class/gpio/export", O_WRONLY);
    if (fd == -1) {
        printf("Unable to open /sys/class/gpio/export\n");
    }

    if (write(fd, "144", 3) != 3) {
        printf("Error to export 144\n");
    }
    close(fd);

    fd = open("/sys/class/gpio/gpio144/direction", O_WRONLY);
    if (fd == -1) {
        printf("Unable to open /sys/class/gpio/gpio144/direction\n");

    }

    if (write(fd, "out", 3) != 3) {
        printf("Error writing to /sys/class/gpio/gpio144/direction\n");
    }
    close(fd);    

    return 0;
}

uint8_t file_buffer[81920]={0x3B};

int write_file(int fd, FILE* fp){
    int num=0;
    int i=0;
    int mode,ret;
    num=fread(file_buffer+1,1,81920,fp);
    printf("file size:%d\n",num);
    
    //transfer(fd,file_buffer,file_buffer,4096); 

    give_some_fucking_sclk_cycles();

    //fd = open("/dev/spidev0.3", O_RDWR);

    //gpio_export();

    //set_cs("0");
    // control cs manually, use a fake spidev to output MOSI
    
    num+=1;
/*
    int SIZE=4095;
    for(i=0;i<num/SIZE;++i){
        printf("cycle:%d\n",i);
        transfer(fd,file_buffer+i*SIZE,file_buffer,SIZE); 
    }
    printf("last cycle num:%d\n",num%SIZE);
    */
    //transfer(fd,file_buffer+i*SIZE,file_buffer,num%SIZE);  

    transfer(fd,file_buffer,file_buffer,num);  
    //set_cs("1");

    return 0;
} 

int rewrite(int fd){
    uint8_t buf[2]={0x3C};
    give_some_fucking_sclk_cycles();
    return transfer(fd,buf,buf,2);   
}

int erase_sram(int fd){
    uint8_t buf[2]={0x05};
    give_some_fucking_sclk_cycles();
    return transfer(fd,buf,buf,2);       
}

int write_disable(int fd){
    uint8_t buf[2]={0x3A};
    give_some_fucking_sclk_cycles();

    int result=transfer(fd,buf,buf,2);     

    return result;
}

uint32_t get_all_codes(int fd){
    // print all code, return status code
    get_codes(fd,READ_ID_CODE);
    get_codes(fd,USER_CODE); 
    return get_codes(fd,STATUS_CODE);
}


int main(int argc,char **argv){
    if (argc != 3){
        printf("error, please set the input filename and spidevice");
        return -1;
    }


    FILE *fp=0;
    int ret,mode,fd;
    ret=mode=fd=0;

    char *filename=argv[2];
    char *device=argv[1];
    fp = fopen(filename,"rb");

    gpio_export();

    give_some_fucking_sclk_cycles();

    set_cs("0");

    give_some_fucking_sclk_cycles();

    set_cs("1");


    printf("open datafile:%s\n",filename);

    fd = open(device, O_RDWR);
    printf("open spidevice:%s\n",device);

    mode = SPI_MODE_0;
    ret = ioctl(fd, SPI_IOC_WR_MODE, &mode);

	if (ret == -1)
		printf("can't set spi mode\n");

	ret = ioctl(fd, SPI_IOC_RD_MODE, &mode);
	if (ret == -1)
		printf("can't get spi mode\n");

    if(mode!=SPI_MODE_0){
        printf("can't set spi mode!\n");
    }

    erase_sram(fd);
    //sleep(1);
    rewrite(fd);

    get_all_codes(fd);

    write_enable(fd);

    write_file(fd,fp);

    write_disable(fd);


    uint32_t status=0;
    status=get_all_codes(fd);

    close(fd);
    fclose(fp);

    if(status & (1<<13)){
        return 0;
    }else{
        return 1;
    }
}

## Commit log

2022-03-27 add docs and images
    [PiPX4.kicad_pcb]
2022-03-27 add teardrop, change the size of drill to 0.45mm
    [PiPX4.kicad_pcb]
2022-03-30 edit spacing to 0.999mm because of JLC
    [PiPX4.kicad_pcb]
2022-04-12 fix u0_rx u0_tx wrong connection issue, fix the hole in V3s GND PAD is too small issue. update to V0.95.
    [PiPX4.kicad_pcb, V3s_core.kicad_sch]
2022-04-16 use LDO to produce 1.2V, to fix fpga voltage issue. fix wrong fpga sch issue, change the pins of fpga. connect fpga SSPI to V3s-spi, so that we can configuare fpag on v3s someday.
    [AutoPilotPi.kicad_pcb, AutoPilotPi.kicad_sch, FPGA.kicad_sch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]
